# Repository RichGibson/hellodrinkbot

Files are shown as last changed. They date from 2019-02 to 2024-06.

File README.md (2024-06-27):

# Hello Drinkbot! 

Cocktail robotics is a fascinating hobby and obsession. 
[Roboexotica](http://roboexotica.at/) was the first, 'and , inevitably, the 
leading festival concerned with cocktail robotics world-wide.'

But you don't have to go to Vienna to make cocktail robots!

Cocktail robotics has traditionally had a fairly steep learning cliff.
There are so many different skills which one can excercise in order to 
create an entertaining robot! 

The Hello Drinkbot project seeks to create a 'hello world' of drinkbots 
to lower the learning cliff so that more people can have fun creating
entertaining ways to get their friends drunk.

The goal is that a person can use the plans here to assemble a functional
drink dispensing robot in an hour or two. You can then build on that 
'hello world' drinkbot in different ways...

Note: not all cocktail robots make drinks, and there are many paths
to cocktail robotics greatness! The premise of Hello Drinkbot is that
having a simple way to make cocktails will bring more people in to apply
their skills and talents and genius to the goal of entertaining us all.

And...cocktail robotics has a history of triggering interesting innovations
in unexpected areas...so dig in! Make a robot. It is fun. And perhaps, a little
messy!
 
..

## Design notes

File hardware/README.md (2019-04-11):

# Hello Drinkbot case designs

This (will be) a selection of different case designs which will work with
the hello drinkbot pumps and electronics.

- [Basic Box](basic_box/README.md) Holds the pumps and electronics and is
suitable as a demonstration, or when used as part of a larger structure.

- [Motor plates](motor_plates/README.md) Various options to hold 4, 7, or
8 pumps.

- [Stand alone](stand_alone/README.md) A basic box that has been extended
a bit so that it stands by itself, with some affordances offered to manage
the dispensing tubing. (still being designed)

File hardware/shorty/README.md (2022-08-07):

# Shorty

Hello Drinkbot: 'Shorty' Shorty

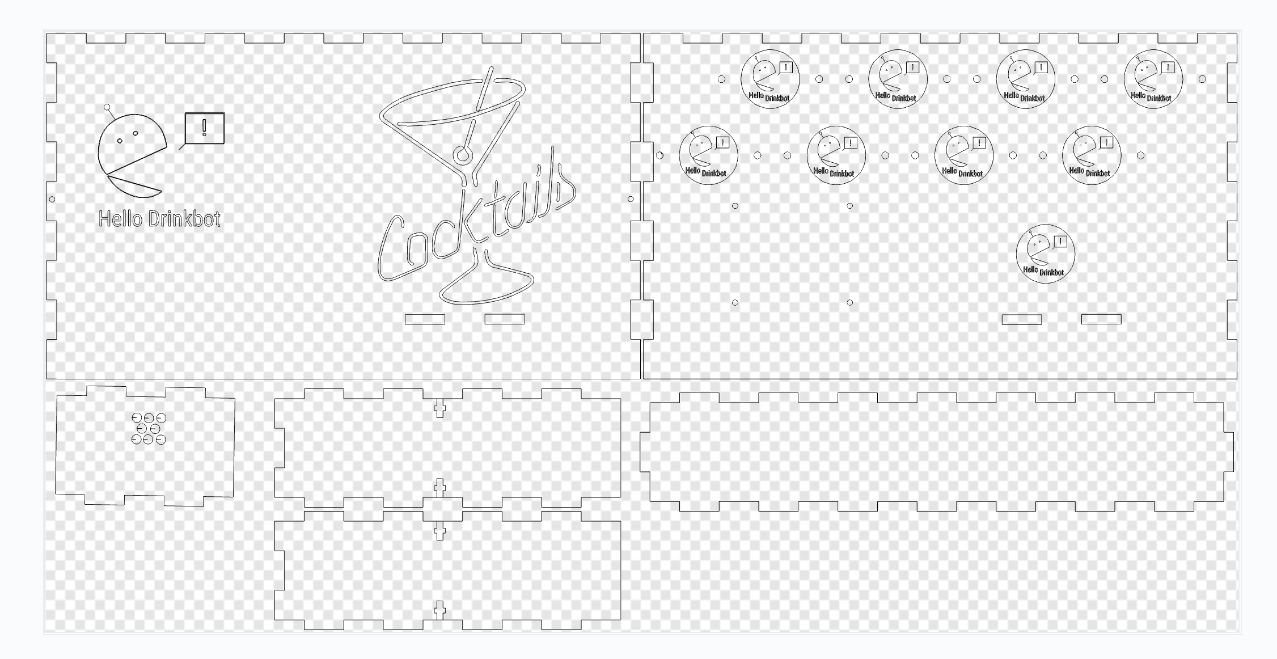
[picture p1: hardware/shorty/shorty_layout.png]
Hello Drinkbot: 'Shorty layout' Shorty


A variant of the Stand alone version, but without the legs. 

Laser cut from 6 mm (1/4") material. Use 4 M3-12mm screws and nuts to fasten 
the case together.

This is a basic box with openings cut for eight peristaltic pumps, and mounting
holes for a Raspberry Pi.

This needs to be placed on a shelf, or other support, or mounted to something 
in order to have it above the supply bottles. There is a piece which holds the 
dispensing tubes in place, and it dispenses out the bottom.

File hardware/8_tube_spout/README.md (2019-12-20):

# 8 Spout Dispenser from Donald Bell

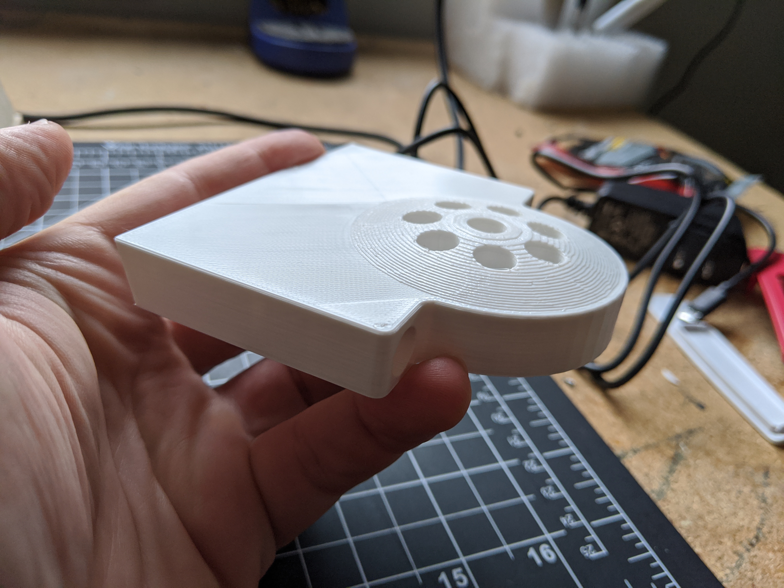
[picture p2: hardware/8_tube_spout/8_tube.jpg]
Hello Drinkbot: 8 tube dispenser 8 tube dispenser

Hello Drinkbot: 8 tube dispenser installed 8 tube dispenser installed

Notes on spout design.

This 8-tube design was modified by Donald Bell from a design shared on Thingiverse by dwmartin805 that accommodates 15 tubes. https://www.thingiverse.com/thing:500062

Like the original the holes are designed to fit 3/16" ID polyethylene barbed tube fittings (McMaster 2808K105) that loosely seat into each hole and can be glued in place for a more permanent design. Being able to remove them makes them a little easier to clean, though.

Because of the initial design of my cocktail robot, I built in a slight angle to where it attaches. I imagine most people will want to throw this into their CAD software and have it attach at a right angle. 

I printed mine in PLA with 10% infill and it's worked fine for my prototype so far, especially since it doesn't take any weight and really just organizes the tubes.

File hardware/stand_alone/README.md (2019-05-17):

# Stand Alone

Hello Drinkbot: Stand Alone Box Stand Alone

Laser cut from 6 mm (1/4") material. Use 24 M3-12mm screws and nuts to fasten 
the case together.

This is a stand alone case with openings cut for eight peristaltic pumps, mounting
holes for a Raspberry Pi, a dispenser, and holes for tubing management.

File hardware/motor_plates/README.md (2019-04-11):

# Motor Plates/Panels

What if you have a bot and you just want to mount some motors? Here are a
selection of plates which you can laser but and mount however works best
for you.

The DXF and SVG files contain what should be the same informtion.

Laser cut from 6 mm (1/4") material. Customize to fit your needs by adding
mounting holes or whatever you need.

# Four pumps in a narror plate

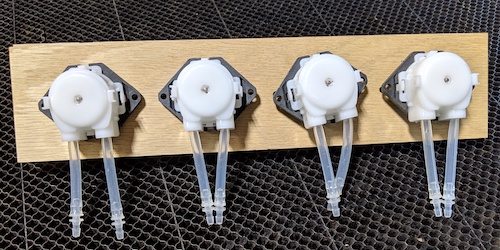
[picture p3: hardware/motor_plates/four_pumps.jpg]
Hello Drinkbot: Four pump motor plate Four pump panel


# Seven pumps in an offset pattern. 

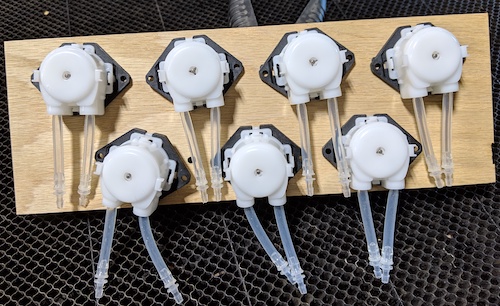
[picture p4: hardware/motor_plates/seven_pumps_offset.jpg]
Hello Drinkbot: Seven pumps offset Seven pumps in an offset pattern


# eight pumps in an offset pattern. 

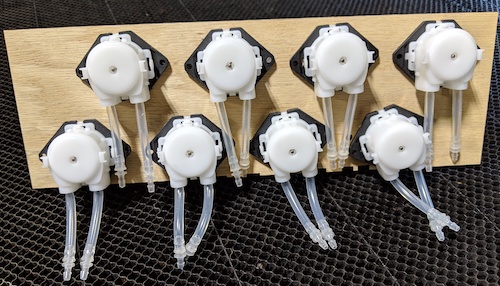
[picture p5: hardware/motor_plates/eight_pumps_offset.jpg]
Hello Drinkbot: Eight pumps offset Eight pumps in an offset pattern


# Eight pumps in a symmetrical pattern. The hoses are routed in an awkward way, 
but this may layout may have utility.
Hello Drinkbot: Eight pumps even Eight pumps in an even pattern

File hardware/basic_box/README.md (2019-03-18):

# Basic Box

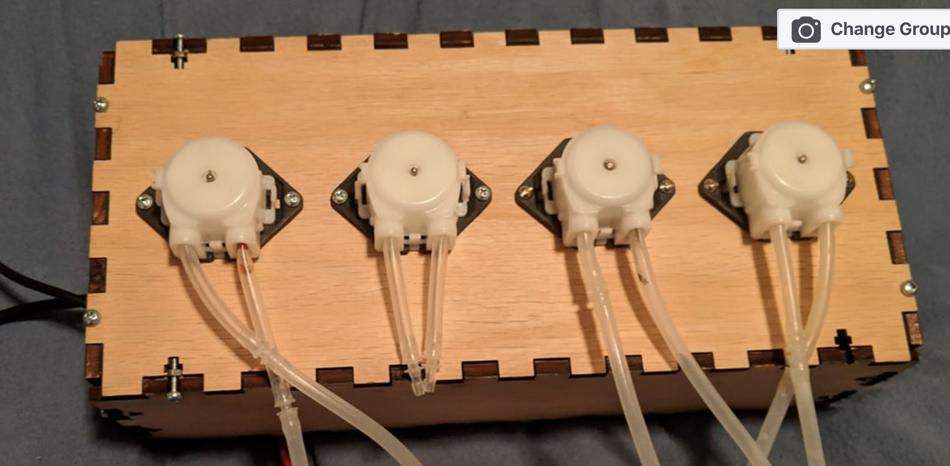
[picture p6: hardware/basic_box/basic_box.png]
Hello Drinkbot: Basic Box Basic box


Laser cut from 6 mm (1/4") material. Use 24 M3-12mm screws and nuts to fasten 
the case together.

This is a basic box with openings cut for four peristaltic pumps, mounting
holes for a Raspberry Pi, and  holes for the a monitor cable, 12 volt power
cable, and USB cable to come out.  

This needs to be placed on a shelf, or other support, or mounted to something 
in order to have it above the supply bottles. No affordance as yet exists for
managing the dispensing side of the tubes.

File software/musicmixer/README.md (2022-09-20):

# Music Mixer 

This is the Music Mixer code. It is based on a Raspberry Pi guitar tuner.
See README-old.md for information on it.

- run `python freqDetect.py` in a linux terminal.

The original frequency detection algorithm can be found here https://benchodroff.com/2017/02/18/using-a-raspberry-pi-with-a-microphone-to-hear-an-audio-alarm-using-fft-in-python/

## Requirements
* Python 3.+
* scipy Python modules. 
* numpy Python modules.
* pyaudio

## Instructions 

I had some troubles. I had the code running, and then I had to go through 
a different process on a new Raspberry Pi. This seemed to work.

Sept 19, 2022

- pip install --upgrade pip
- sudo apt-get install portaudio19-dev
(on my Mac it was brew install portaudio)
- sudo apt-get install python3-scipy
- pip install pyaudio

Possibly also libatlas-base-dev?

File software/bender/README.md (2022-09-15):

# Bender the Vender

- Do you want a Martini, or fuck off. 

## Installation

    $ sudo su 
    # Requirements, the requirements.txt has a lot of unneeded things.
    # So either install them, or just try running bender.py and install
    # libraries as they are missing.
    $ pip install -r requirements.txt
    $ pip install python-vlc (should be in requirements)
    $ sudo crontab -e 

    add: 

    @reboot python /home/pi/hellodrinkbot/software/bender/bender.py

(There is a bit of tension between writing docs to be a contemporaneous 
account of the process, and notes that will help someone else follow your
path. You don't know what you need to know when you write the notes. How
much of the journey do you keep? Depends on how much time you have to edit
the documents)

## Next Steps

### Electronics
1. done mount 3rd switch and wiring. Slightly harder because the 3rd button is installed on the front plate
1. done mount 2 pumps, towards sides to provide room for head mounting options
1. done mount pi and button board and connect to motors and buttons
1. done mount leds. They are going to be obscured a bit by the arms. Drill hole, it gets too hot for hot glue.
1. done pi and pump power
1. speaker in the head. Can cut off the base of the speakers

### Case
1. done glue top and sides of case
1. done close up the button box
1. mount dispenser holder 
1. mount tubing
1. cover pump holes

1. do the arms need to come off for packing? If so need to do things a bit different.

1. Figure out head mounting

1. Make it dirty label
1. (Christine) finish the body. I think the Mouth is the big remaining issue. 

1. document all of the wires and controllers

### Final!

1. calibrate martini and dirty dispense amounts. Light pours, let people adjust their cocktail size by the number of times they push the buttons

1. Martini glass, toothpicks, olives
1. Olive juice

## Software

Pour martini from one pump, and olive juice to make it dirty from a second, 
premixed martinis, so just use my own code, no Bartendro

## Hardware

Two pumps, three buttons, Raspberry Pi, motor hat, and button board. Amazing body 
of Bender made by Christine.

## Sounds

Bender sound clips from JAYUZUMI.COM.mp3. Assigned a few sound clips to 'good'
(played when the user selects 'Martini,' 'bad' (when they select Fuck off),
and 'dirty' (when they make it dirty).

I have ~89 sound clips. I've added the clips I am using to the github repository.

## Log

### Sept 13th, 2022

Three buttons work. Reasonable sounds are played. The pumps are probably
working.

### Sept 7th, 2022

Did brain surgery, Ukranian Roulette gets the old pi. Bender has a 3b,
and a motor hat with header pins soldered on for the buttons and led's.

And booted up into bender.py, a copy of ukr.py, and the buttons blink back 
and forth just as they should.

### Sept 5th, 2022

Soldered a hat for an old raspberry pi, and buttons and connected
pumps and it all worked using the ukr.py code. So, copy that code
and reconfigure it to be Martini or fuck you.

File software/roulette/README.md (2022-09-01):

# Ukrainian Roulette

## Installation

    $ sudo su 
    $ pip install -r requirements.txt
    $ sudo crontab -e 

    add: 

    @reboot python /home/pi/hellodrinkbot/software/roulette/ukr.py

## Aug 30, 2022

Christine and I served drinks from it and everything worked. Dang!

## Aug 26, 2022

Strip out the need for Bartendro. We have four pumps, we don't need all 
of that code. Especially since I don't understand it.

Aug 25, 2022

New buttons are installed, and work. And I modified Bartendro a bit. And 
now if you press button 2 and then button 1 it is fine, but if you 
go the other way bartendro stops the second pump when the first one
finishes dispensing.

Also, the case is beautiful. The Burroughs-Apple montage is amazing.

And I now understand why Christine liked the name. It is not 'yay
Ukraine' it is 'we hate Russia, so it is like Freedom Fries' or 
'Victory Cabbage.'  Just reflexive erasure of the enemy and disfavored

Aug 6, 2022
Based on an idea of Spencer's at the 'Drinkbot Hackathon and Networking'
event May 12th, 2018

A bot appears. There are two buttons on the top. One labeled with
one figure, the other with two figures.

One or two people put shot glasses under the robot, in the dispensing
area. And then a button is pushed.

One or two shots are poured. Probably 1/2 oz shots.

And the participants drink.

Most of the shots are as expected. But one out of six is something less
attractive. Right now we are thinking Malort.

That's it...

## Hardware

Four pumps, thinking a custom box, two buttons, Raspberry Pi and motor
hat.

## Software

Running Hello Drinkbot image, but a custom bit of python.

## Decoration

Thinking of a picture of William Burroughs with an apple on his head on
the front. If you know, you know. I printed an assortment of pictures, and of
apples at various sizes, and Christine ran with it. Yay.

The top is painted with Ukranian colors.  Christine explained that this was funny
in the same way that 'Freedom Fries' are funny. We have a geopolitical bruhaha (disregarding
the legitimacy of the tiff) and we need to rename things that originate in the 'other'
nation.

Freedom Fries. Liberty cabbage in place of saurkraut. etc.

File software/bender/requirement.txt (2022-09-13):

Adafruit-bitfield==1.5.1
Adafruit-Blinka==8.2.0
adafruit-circuitpython-busdevice==5.2.1
adafruit-circuitpython-motor==3.4.3
adafruit-circuitpython-motorkit==1.6.9
adafruit-circuitpython-pca9685==3.4.4
adafruit-circuitpython-pixelbuf==1.1.7
adafruit-circuitpython-register==1.9.11
adafruit-circuitpython-seesaw==1.11.5
adafruit-circuitpython-typing==1.7.2
Adafruit-GPIO==1.0.3
Adafruit-MotorHAT==1.4.0
Adafruit-PlatformDetect==3.27.0
Adafruit-PureIO==1.1.9
Adafruit-seesaw==1.0
arandr==0.1.10
astroid==2.5.1
asttokens==2.0.4
automationhat==0.2.0
beautifulsoup4==4.9.3
blinker==1.4
blinkt==0.1.2
buttonshim==0.0.2
Cap1xxx==0.1.3
certifi==2020.6.20
chardet==4.0.0
click==7.1.2
colorama==0.4.4
colorzero==1.1
cryptography==3.3.2
cupshelpers==1.0
dbus-python==1.2.16
distro==1.5.0
docutils==0.16
drumhat==0.1.0
envirophat==1.0.0
ExplorerHAT==0.4.2
Flask==0.10.1
Flask-Login==0.3.2
Flask-SQLAlchemy==2.5.1
fourletterphat==0.1.0
gpiozero==1.6.2
html5lib==1.1
idna==2.10
isort==5.6.4
itsdangerous==1.1.0
jedi==0.18.0
Jinja2==2.11.3
lazy-object-proxy==0.0.0
logilab-common==1.8.1
lxml==4.6.3
MarkupSafe==1.1.1
mccabe==0.6.1
microdotphat==0.2.1
mote==0.0.4
motephat==0.0.3
mypy==0.812
mypy-extensions==0.4.3
numpy==1.19.5
oauthlib==3.1.0
olefile==0.46
pantilthat==0.0.7
parso==0.8.1
pexpect==4.8.0
pgzero==1.2
phatbeat==0.1.1
pianohat==0.1.0
picamera==1.13
piglow==1.2.5
pigpio==1.78
Pillow==8.1.2
psutil==5.8.0
pycairo==1.16.2
pycups==2.0.1
pyftdi==0.54.0
pygame==1.9.6
Pygments==2.7.1
PyGObject==3.38.0
pyinotify==0.9.6
PyJWT==1.7.1
pylint==2.7.2
pyOpenSSL==20.0.1
pyserial==3.5b0
pysmbc==1.0.23
python-apt==2.2.1
python-memcached==1.59
python-vlc==3.0.16120
pyusb==1.2.1
rainbowhat==0.1.0
readchar==4.0.0
reportlab==3.5.59
requests==2.25.1
requests-oauthlib==1.0.0
responses==0.12.1
roman==2.0.0
rpi-ws281x==4.3.4
RPi.GPIO==0.7.0
RTIMULib==7.2.1
scrollphat==0.0.7
scrollphathd==1.2.1
Send2Trash==1.6.0b1
sense-hat==2.2.0
simplejson==3.17.2
six==1.16.0
skywriter==0.0.7
sn3218==1.2.7
soupsieve==2.2.1
spidev==3.5
SQLAlchemy==1.4.40
ssh-import-id==5.10
sysv-ipc==1.1.0
thonny==3.3.14
toml==0.10.1
touchphat==0.0.1
twython==3.8.2
typed-ast==1.4.2
typing-extensions==3.7.4.3
unicornhathd==0.0.4
urllib3==1.26.5
webencodings==0.5.1
Werkzeug==1.0.1
wrapt==1.12.1
WTForms==3.0.1

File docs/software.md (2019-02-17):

# Using Hello Drinkbot with Python

# Getting Started

# Using Hello Drinkbot with Node Red

- install the python motor hat libraries

# Getting Started

- Node Red is installed by default, but you need some extra packages

- Install the node software for the motor hat
  - sudo apt-get update
  - sudo apt-get install npm
  - npm install --save motor-hat

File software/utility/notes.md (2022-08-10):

Notes March 11, 2021

update July 28, 2022 - this continues to work.

In bartendro 3 and 4 and 7 and 8 are inverted. But they 
work in order in this pumptest.

This will excercise 16 pumps, turning each on for 1 second.
python3 ./pumptest16.py 1

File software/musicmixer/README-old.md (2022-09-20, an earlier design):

# RPiPitch

https://github.com/katrinamo/RPiPitch

This directory contains the code for a Raspberry Pi guitar tuner based on an FFT pitch detection algorithm. The code that should be executed is the freqDetect.py file. To execute, run `python freqDetect.py` in a linux terminal.

The original frequency detection algorithm can be found here https://benchodroff.com/2017/02/18/using-a-raspberry-pi-with-a-microphone-to-hear-an-audio-alarm-using-fft-in-python/

This project modifies the fft algorthm, but it's based on the source found above.

## Requirements
* Python 2.7
* scipy Python modules. 
* numpy Python modules.
* matplotlib Python modules.

## Instructions

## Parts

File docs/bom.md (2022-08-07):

# Hello Drinkbot Bill of Materials

|item|cost|count|total cost|note|url
|----|----|-----|---|----|---|
|Raspberry Pi|38|1|38.00||https://www.amazon.com/gp/product/B0791YL351/ref=oh_aui_search_asin_title?ie=UTF8&psc=1
|Motor Hat|21.88|1|21.88||https://www.amazon.com/Adafruit-Stepper-Motor-HAT-Raspberry/dp/B00TIY5JM8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
|Pumps|9.8|4|39.20|cheaper at AliExpress|https://www.aliexpress.com/item/Peristaltic-Pump-Head-Dosing-Pump-Head-Tubing-Hose-Pump-Aquarium-Lab/32770860268.html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
|12 volt power supply|10|1|10.00|2.5 amps is probably good enough
|sd card|10|1|10.00|various options
|tubing|8.19|1,8.19|You don't need this much - we can share!|https://www.amazon.com/gp/product/B01F4BJBA4/ref=ppx_yo_dt_b_asin_title_o06__o00_s00?ie=UTF8&psc=1
|wood or acrylic|10,||10.00|various options. 1/4" birch plywood is nice
|m3 12mm screws and nuts|||
|standoffs
|wire
|crimp connectors||||or you can solder the motors
||||||
|Total|||137.27|A work in progress. Suggestions welcome

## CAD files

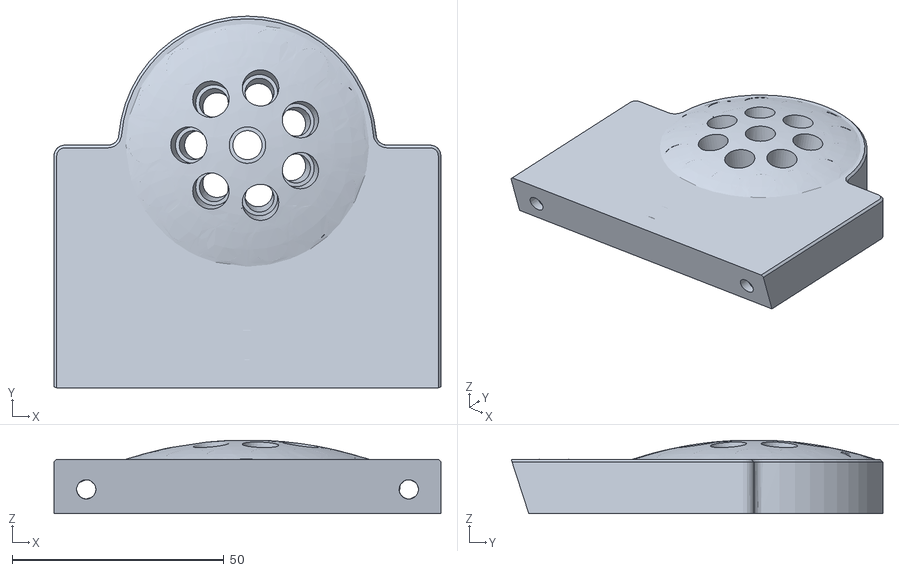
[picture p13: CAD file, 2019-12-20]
hardware/8_tube_spout/8_tube_dispenser.stl
91.4 x 87.8 x 17.3

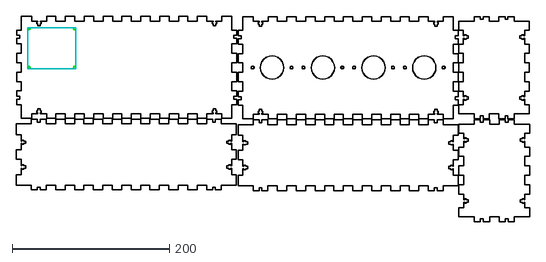
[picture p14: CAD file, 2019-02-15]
hardware/basic_box/frame_2019-02-10.dxf
653.2 x 261.3

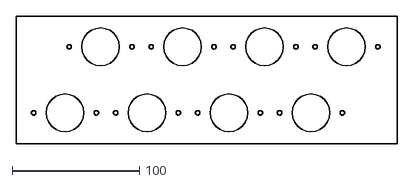
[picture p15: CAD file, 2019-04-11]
hardware/motor_plates/eight_pumps_offset.dxf
300.0 x 100.0

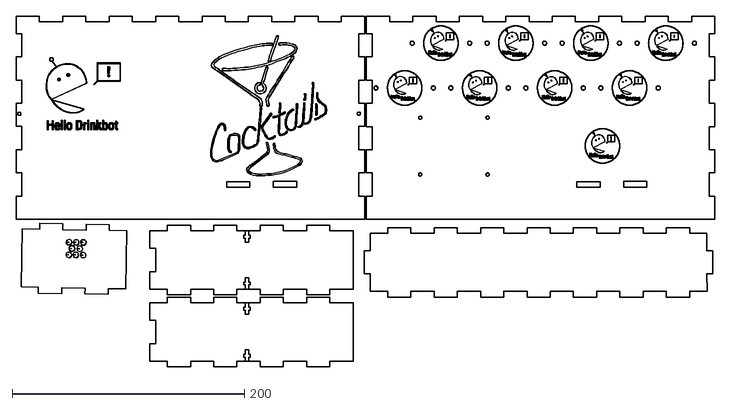
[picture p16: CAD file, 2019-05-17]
hardware/shorty/shorty.dxf
601.6 x 302.0

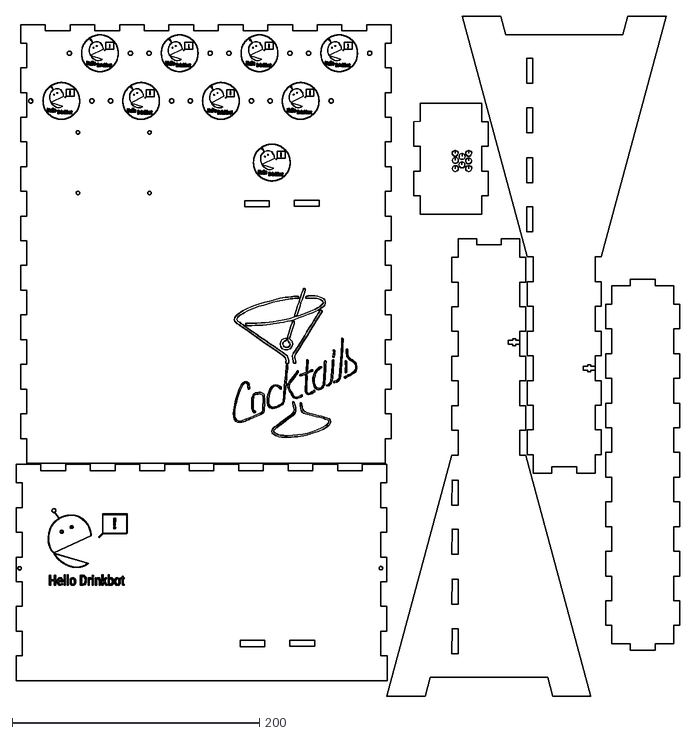
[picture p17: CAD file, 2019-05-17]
hardware/stand_alone/stand_alone.dxf
537.0 x 550.3

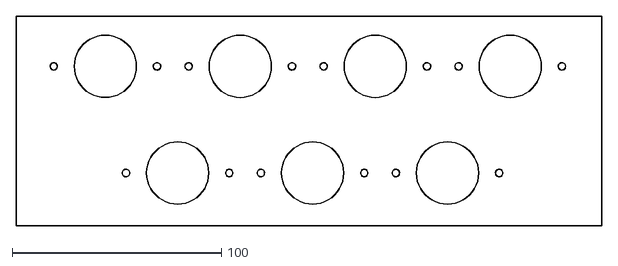
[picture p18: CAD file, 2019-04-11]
hardware/motor_plates/seven_pump_offset.dxf
280.0 x 100.0

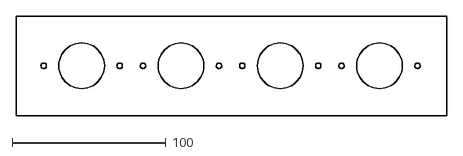
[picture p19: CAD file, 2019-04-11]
hardware/motor_plates/four_pump.dxf
280.0 x 65.0

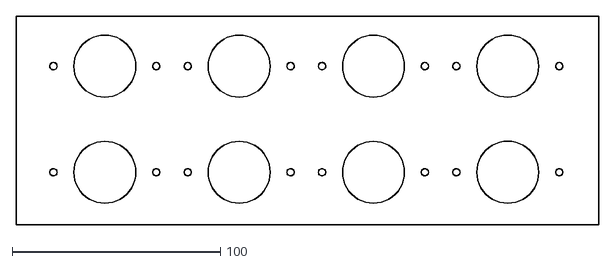
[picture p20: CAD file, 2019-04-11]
hardware/motor_plates/eight_pumps_even.dxf
280.0 x 100.0

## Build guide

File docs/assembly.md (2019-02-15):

# Common Open Cocktail Robotics Stack

Description: A Raspberry pi dispensing robot with four pumps, controlled 
either from the command line or Node Red. 

Electrical

- Raspberry Pi 
- Motor Shield (will work with the older ones with a 2x13 header from adafruit) there are lots of underutilized older raspberry pi's!
- wires to the pumps
- Peristaltic Pumps

Physical

- Laser cut case
- fluid aggregation point, hose management

Software

- Command line interface-exists
- Node Red interface with RESTful endpoints  (tk)

Design files

- frame_2019-02-10.dxf

Assembly

- customize the case design as desired
- laser cut it onto 1/4"/6mm plywood or acrylic

- copy Raspberry Pi SD card image, put in pi
- boot up and customize it as desired (probably the wifi essid is the main thing)

default login username pi password raspberry

powering pi: you need to connect the pi to usb power, it is not recommended to 
use the motor power for the pi.

- [Assemble the motor hat](https://learn.adafruit.com/adafruit-dc-and-stepper-motor-hat-for-raspberry-pi/overview)

- mount the pi onto the back plate
Todo: need to figure this out. possibly plastic screws, untapped spacers, and 
plastic nuts on the top? there is not really clearance for nuts on all four 
positions on the top`o

- attach the 12 volt power to the motor shield

- install pumps into face plate with 8 screws and nuts (m3-12mm would work fine

- crimp connectors, or solder, 8 wires onto the pumps

- attach motor wires to motor hat, and put the hat on the pi

Motor hat needs 1 or two standoffs or spacers of its' own 

- power up and test before assembling the case

- assemble the case with m3-12mm screws and nuts

- attach tubing and figure out where to dispense

- connect to the pi as an access point

- design something entertaining.

- write some software...(a simple matter of programming)

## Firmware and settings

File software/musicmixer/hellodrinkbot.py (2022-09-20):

# hellodrinkbot.py - library for hello drinkbot toys

import sys
import os
import pdb
import time
import atexit
import random
from datetime import datetime
import threading


try:
    from adafruit_motorkit import MotorKit
    emulation=0
except:
    # no motorkit
    emulation=1

class HelloDrinkbot():
    def __init__(self, **kwargs):
        """ Keyword arguments include:
            emulation   - do we have a pi and a motor hat?
        """
        self.mh1 = MotorKit()
        atexit.register(self.turnOffMotors)

        # I'm going to just run wild with unnamed arguments 
        for k, v in kwargs.items():
            setattr(self, k, v)

        # mapping pumps 1-8, ignore 0, because adjusting just
        # messes me up and leads to off by one
        self.dispense_flag=[0 for f in range(9)]
        self.buttons ={} 
        try:
            import RPi.GPIO as GPIO # Import Raspberry Pi GPIO library
            GPIO.setwarnings(False) # Ignore warning for now
            GPIO.setmode(GPIO.BCM) # GPIO.BCM or GPIO.BOARD

        except Exception as e:
            print(e)
            print('Raspberry pi not responding, continuing in emulation mode')
            self.emulation=1
        self.m = []
        try:
            self.m.append(self.mh1.motor1)
            self.m.append(self.mh1.motor2)
            self.m.append(self.mh1.motor3)
            self.m.append(self.mh1.motor4)
        except Exception as e:
            print(e)
            print("can't add motors in HelloDrinkbot.__init__()")
            sys.exit(2)

    def motor_on(self, pump, pumptime):
        print('\tStarting pump %s for %i seconds' % (pump, pumptime))
        self.dispense_flag[pump]=1
        #motor=0,1,2,3
        motor = pump // 2
        # direction = -1 or 1
        if pump % 2 == 0:
            direction = -1
        else:
            direction = 1
        self.m[motor].throttle = direction
        time.sleep(pumptime)
        self.m[motor].throttle = 0
        self.dispense_flag[pump]=0
        print('\tStopping pump %s after %i seconds' % (pump, pumptime))


    def dispense(self,pump, pumptime):
        '''
        pump 1-8 odd numbers are -1 even numbers 1, I guess.
        pump 1 self.m[0].throttle=-1
        pump 2 self.m[0].throttle=1
        pump 3 self.m[1].throttle=-1
        pump 4 self.m[1].throttle=1
        pump 5 self.m[2].throttle=-1
        pump 6 self.m[2].throttle=1
        pump 7 self.m[3].throttle=-1
        pump 8 self.m[3].throttle=1
        '''
        print(pump,time)
        print('dispense() pump %d time %d ' % (pump, pumptime))
        # check if we are dispensing on our pump, or our pump sister.
        # if not, set the dispense flag and call motor_on 
        if  self.dispense_flag[pump]==0:
            x=threading.Thread(target=self.motor_on, args=(pump, pumptime))
            x.start()



    def turnOffMotors(self):
        self.mh1.motor1.throttle = None
        self.mh1.motor2.throttle = None
        self.mh1.motor3.throttle = None
        self.mh1.motor4.throttle = None


#### Tests below here
import unittest
class TestHelloDrinkbot(unittest.TestCase):
    def test(self):
        self.assertEqual(1,1) 

    def test_imports(self):
        try:
            from adafruit_motorkit import MotorKit
            emulation=0
        except:
            # no motorkit
            emulation=1
            self.assertEqual(1,0,"Can't import motorkit")

    def test_motors(self):
        # does self.turnOffMotors work?
        hd=HelloDrinkbot(emulation=0)
        hd.mh1.motor1.throttle=-1
        self.assertEqual(-1,hd.mh1.motor1.throttle)
        time.sleep(.5)
        hd.turnOffMotors()
        self.assertEqual(None,hd.mh1.motor1.throttle)

if __name__ == '__main__':
    print('Running hellodrinkbot library tests')
    unittest.main()

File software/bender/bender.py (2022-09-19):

# Martini or fuck you.

# Todo: 
# - play bite my shiny metal ass if you pick the 'fuck you' button
# - hook pump or two pumps up to pour martini if you press the martini button

import pdb
import sys
import vlc
import os
from time import sleep
import board
import digitalio
from adafruit_seesaw.seesaw import Seesaw
from adafruit_seesaw.digitalio import DigitalIO
from adafruit_seesaw.pwmout import PWMOut
import random

from threading import Thread, Event
import urllib.request

# For most boards.
i2c = board.I2C()

# The Seesaw board fails on start up, so just retry up to five times.
# The error I get:
# RuntimeError: Seesaw hardware ID returned (0xc3) is not correct! Expected 0x55 or 0x87. Please check your wiring.

print('Initializing Seesaw board')
cnt = 0
while cnt < 5:
    try:
        arcade_qt = Seesaw(i2c, addr=0x3A)
        cnt = 99
    except:
        cnt+=1
        print('\tSeesaw hardware error...waiting to try again. cnt: ', cnt) 
        sleep(2)
        pass

# what is played when you press 'make it dirty'

dirty_files = [
        "file:////home/pi/hellodrinkbot/software/bender/sound/HERE COMES VIOLENCE - AUDIO FROM JAYUZUMI.COM.mp3",
        "file:///home/pi/hellodrinkbot/software/bender/sound/YOU DON'T HEAR ME NOT COMPLAINING - AUDIO FROM JAYUZUMI.COM.mp3",

    ]

# what is played for the 'fuck you' button
bad_files = [
        "file:////home/pi/hellodrinkbot/software/bender/sound/NOSE BLOW - AUDIO FROM JAYUZUMI.COM.mp3",
        "file:////home/pi/hellodrinkbot/software/bender/sound/bite.mp3",
    ]

# nice things, supportive things, dialoque you get when you make the correct choice.
good_files = [
        "file:////home/pi/hellodrinkbot/software/bender/sound/GOT IT - AUDIO FROM JAYUZUMI.COM.mp3",
        "file:////home/pi/hellodrinkbot/software/bender/sound/HEY, HERE'S AN IDEA - AUDIO FROM JAYUZUMI.COM.mp3",
        "file:///home/pi/hellodrinkbot/software/bender/sound/YOU GOT IT GENIUS - AUDIO FROM JAYUZUMI.COM.mp3",
        "file:///home/pi/hellodrinkbot/software/bender/sound/THIS PLACE HAS CLASS - AUDIO FROM JAYUZUMI.COM.mp3",
        "file:///home/pi/hellodrinkbot/software/bender/sound/THIS WILL TEACH THOSE FILTHY BASTARDS WHO'S LOVEABLE - AUDIO FROM JAYUZUMI.COM.mp3",
        "file:///home/pi/hellodrinkbot/software/bender/sound/MAYBE IF YOU CLEAN UP FIRST - AUDIO FROM JAYUZUMI.COM.mp3",
    ]




def load_media(files):
    media = []
    # try preloading files
    for file in files:
        # Grab file extension
        ext = (file.rpartition(".")[2])[:3]
        found = False
        # Test if url is a local file or remote
        if file[:4] == 'file':
            if os.path.isfile(file[7:]):
                found = True
            else:
                print ('Error: File ', file[7:], ' Not found')
                continue
        else:
            try:
                r = requests.get(file, stream=True)
                found = r.ok
            except ConnectionError as e:
                print('failed to get stream: {e}'.format(e=e))
                continue
        if found:
            #Media = Instance.media_new(file)
            media.append(Instance.media_new(file))
            Media_list = Instance.media_list_new([file])
            media[0].get_mrl()
            player.set_media(media[0])
    return media

Instance = vlc.Instance()
player = Instance.media_player_new()
player.audio_set_volume(200)

print ("Loading audio files")
good_media = load_media(good_files)
bad_media = load_media(bad_files)
dirty_media = load_media(dirty_files)

# So media is now a list, with the mp3 files listed in files[]
# and we can do player.set_media(media[index]) and then play that.
# so clean it up and ship it?
# maybe good_media and bad_media


def play(name, lst):
    # pick an audio file from the passed list and play it
    x = random.randint(0,len(lst)-1)
    print('\twhat %s media to play %i' % (name, x))
    media = lst[x]
    player.set_media(media)
    player.audio_set_volume(200)
    if player.play() == -1:
        print('error playing %s',name)



# initialize buttons[] and leds[]
# Button pins in order (1, 2, 3, 4)
button_pins = (18, 19, 20, 2)
buttons = []
for button_pin in button_pins:
    button = DigitalIO(arcade_qt, button_pin)
    button.direction = digitalio.Direction.INPUT
    button.pull = digitalio.Pull.UP
    buttons.append(button)

# LED pins in order (1, 2, 3, 4)
led_pins = (12, 13, 0, 1)
leds = []
for led_pin in led_pins:
    led = PWMOut(arcade_qt, led_pin)
    leds.append(led)

try:
    from adafruit_motorkit import MotorKit
    emulation=0
except:
    # no motorkit
    emulation=1 

from bender_lib import Bender as Bender    
bender = Bender(emulation=0)

# Todo: want to turn off the light of a dispenser that is not dispensing
# there is a race condition, which is why in this loop I turn the led off
# and then on, so when it is interrupted it doesn't interfere with dispense()
# turning the light on.
def blink(foo):
    '''blink leds until stopped. Why? '''
    while True:
        if event.is_set():
            sleep(1)
            continue
        for num in (0,1):
            sleep(.4)
            leds[num].duty_cycle = 0 
            leds[num+2].duty_cycle = 0 
            sleep(.4)
            leds[num].duty_cycle = 65535
            leds[num+2].duty_cycle = 65535 

event = Event()
ledthread = Thread(target=blink, args=(0,))
ledthread.start()

def dispense(num, bender):
    # whoops, race condition
    event.set()
    print('\tstart dispense: ', num)
    leds[num].duty_cycle = 65535
    # todo: does urllib block? yes. So it is perfect

    # todo: need to determine the pump.
    # my 1,3,5,7 maps to dispensers 0,2,4,6
    # 0,2 - good stuff
    # 4,6 - You never expect the Malort
    # map 0 and 1 to good and bad

    # which pump should we use? 
    # for bender it is pump 1 or 'fuck you'

    if num==0:
        pump = 0
        play('good', good_media)
        print('\tdispensing  a martini to pump %i ' % pump)

        # TODO: move this somewhere reasonable
        ml = 10 # how big is the drink? 10 is tiny for testing.
        SECONDS_PER_ML = 18/100. # huh?
        delay = ml*SECONDS_PER_ML

        # dispense our beverage...
        bender.m[pump].throttle=-1
        sleep(delay)
        bender.m[pump].throttle=0
    if num==1:
        play('bad', bad_media)
        print('\tNo Martini!')
    if num==2:
        pump = 1
        play('dirty', dirty_media)
        print('\tdispensing  some olive juice pump %i ' % pump)

        # TODO: move this somewhere reasonable
        ml = 10 # how big is the drink? 10 is tiny for testing.
        SECONDS_PER_ML = 18/100. # huh?
        delay = ml*SECONDS_PER_ML

        # dispense our beverage...
        bender.m[pump].throttle=-1
        sleep(delay)
        bender.m[pump].throttle=0

    leds[num].duty_cycle = 0 
    print('\tend dispense: ', num)
    flags[num]=0
    # I want to restart ledthread
    event.clear()
       
flags=[0,0,0]
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

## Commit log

2019-02-15 initial files
    [frame_2019-02-10.dxf]
2019-02-15 added bill of materials
2019-03-18 Added README for the basic box design, and moved the basic box files into their own directory.
    [frame_2019-02-10.dxf]
2019-03-18 Added README and start of the stand alone case
2019-03-24 added new motor panels
    [eight_pumps_even.dxf, eight_pumps_offset.dxf, four_pump.dxf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]
2019-03-24 added motor plates to the readme
2019-04-16 from box maker http://jeromeleary.com/laser/
    [laser.dxf]
2019-04-19 stand_alone work in progress
    [stand_alone_wip3.dxf]
2019-05-01 close to final in stand_alone_wip6
    [stand_alone_wip6.dxf]
2019-05-16 Added readme and image for the shorty case
2019-05-17 Added svg and dxf for Shorty
    [shorty.dxf]
2019-05-17 added current stand alone
    [laser.dxf, stand_alone.dxf, stand_alone_wip3.dxf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]
2019-12-20 Added 8 tube dispenser from Donald Bell
    [8_tube_dispenser.stl]
2019-12-20 Added 8 Tube README
2021-03-11 pumptest16.py uses python3 and the new motor kit library. It turns 16 pumps on, in order.
2021-03-24 A variation for 1/8 material
2022-08-07 The button interface works on the pi. Yay.
2022-08-10 too many changes to keep track of. ukr.py now does threading. Yay. Shocking1.py is a start towards controlling the digital pot. button_test.py tests buttons. etc.
2022-08-12 pumptest_all turns all motor hats forward, then all backwards.
2022-08-15 Too much to keep track of. Flailing with buttons that are flaky, both hardware and my code
    [button_test.py, buttons.py, hellodrinkbot.py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]
2022-08-15 test buttons
2022-08-23 test adafruit button/led board
2022-08-26 button_ukr_wip.py works more or less by calling Bartendro. There is an apparent Bartendro quirk/bug.
2022-08-27 ukr_lib - a library of sorts to control motors for Ukranian Roulette
2022-09-01 Now the LEDs blink to show that the robot has booted up, and they stop when a button is pushed. I would like to have them blink whenever a dispense is not running, but I don't really understand threa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
2022-09-05 Run motor 1 in forward and reverse
    [pumptest2.py]
2022-09-06 Added comment. My ml to time mapping is wrong, pouring much less than I thought.
    [ukr.py]
2022-09-08 Updated requirements to resolve Dependabot alerts. And expanded my sound testing for Bender.
    [sound_test2.py]
2023-11-27 The app is incomplete, but it exists and displays an image of a bird with three possible bird names to choose from
    [bird_list.csv, birds_all.csv, birds_quiz.csv]
2023-11-28 moved Vogelroboter to its' own repository
    [bird_list.csv, birds_all.csv, birds_quiz.csv]
